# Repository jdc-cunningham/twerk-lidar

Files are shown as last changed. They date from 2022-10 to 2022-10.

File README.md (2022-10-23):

### Twerk Lidar Robot
A robot that utilizes onboard IMU and single-point lidar to navigate the world

#### With actual "Lidar"
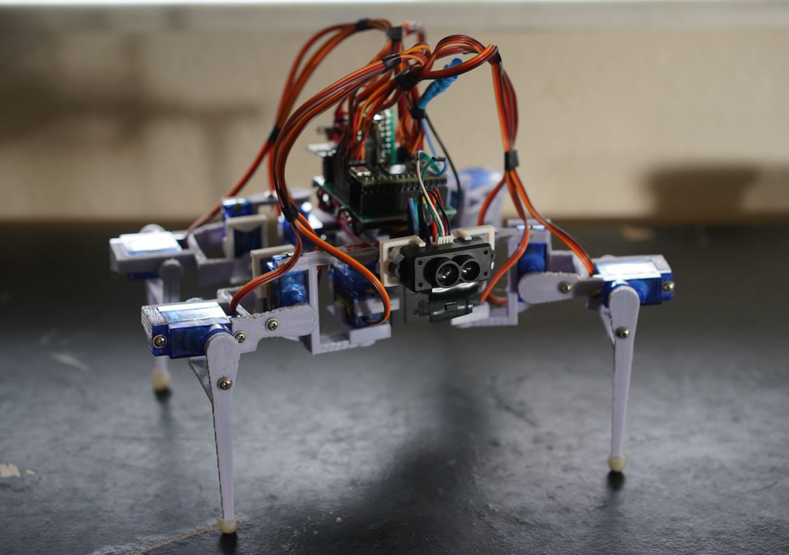
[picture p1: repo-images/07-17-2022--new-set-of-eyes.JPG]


#### Initial sensor setup
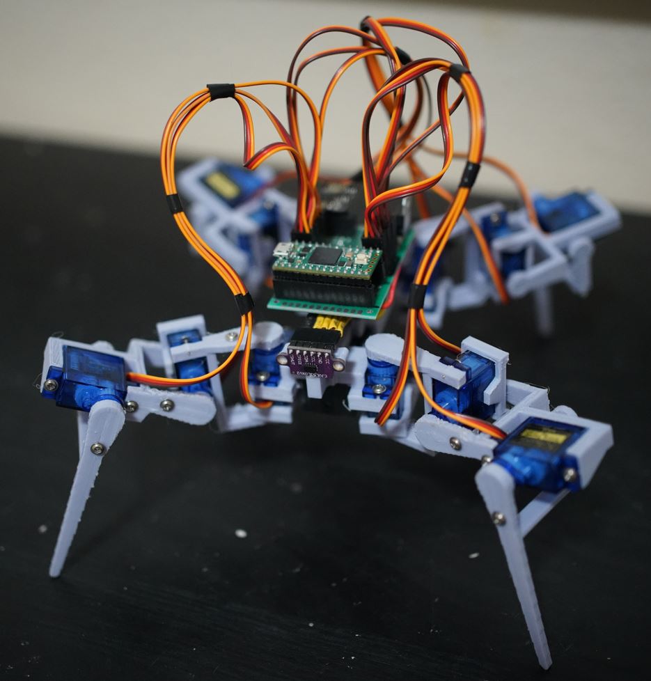
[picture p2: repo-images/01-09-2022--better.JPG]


### Project status (incomplete)

### What is it


Example depth map:
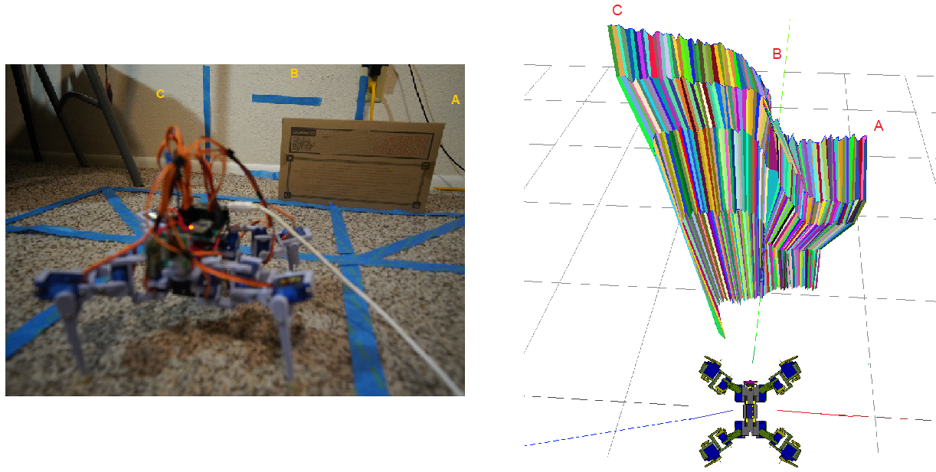
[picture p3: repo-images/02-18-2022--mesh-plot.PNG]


### Sensors

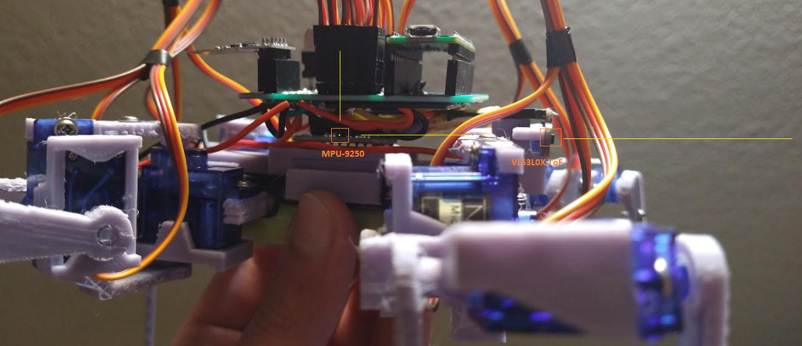
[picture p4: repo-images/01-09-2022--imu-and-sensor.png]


### Schematic

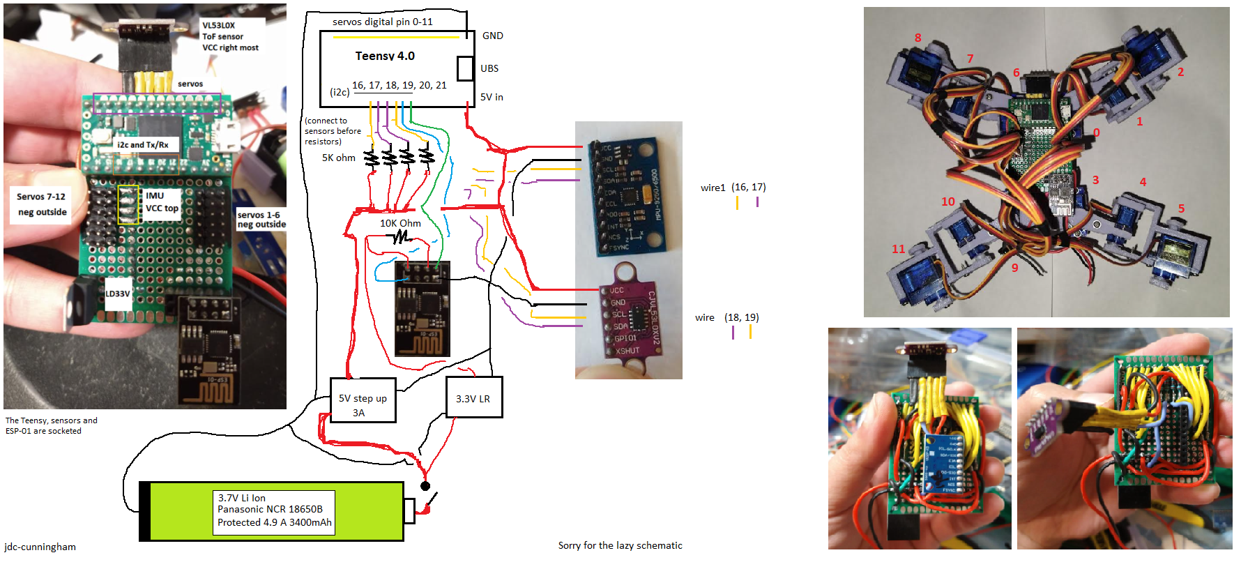
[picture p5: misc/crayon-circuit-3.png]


### Also Has 3D export/import from SketchUp to ThreeJS (GLB)

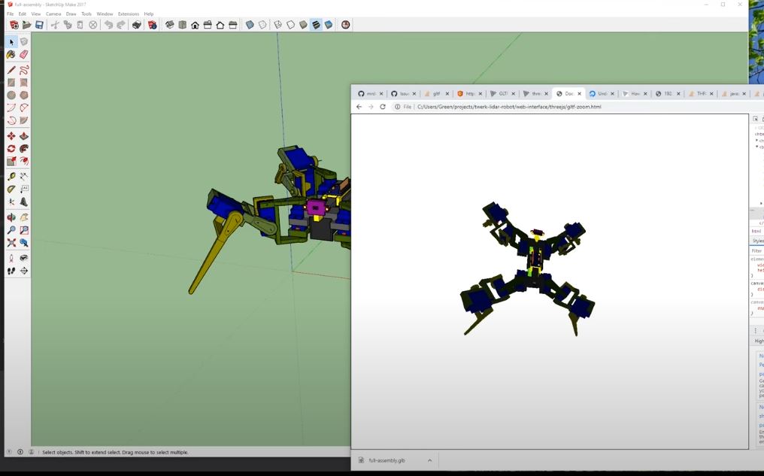
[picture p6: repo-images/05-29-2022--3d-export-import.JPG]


Uses Khronos glTF SketchUp plugin

### Unit cost estimate: $100+
This is a breakdown of the most expensive stuff on the robot. Does not include the little 3.3V regulator, the 3D printer itself, filament, proto-board, wire, etc...

* $24.00 - 12 x 9g servos
* $20.00 - Teensy 4.0
* $14.00 - MPU-9250
* $14.00 - MPS mEZD41503A-A 5V @ 3A DC/DC converter
* $11.00 - ToF sensor
* $10.00 - NCR 18650B 3.4 Ah 4.9A Protected Button Top Battery
* $3.25 - ESP-01

Upgrades (extra cost)
* $40.00 - TFMini-s Lidar
* $120 - 12 x MG90D metal gear servos

#### Note:

If you upgrade to the MG90D servos, you will need to add a separate power supply eg. MT3608 to power the Teensy so that the servos do not reset it while booting. Otherwise the legs will flail around on start up.

### Disclaimer - do not reproduce this project
While I have provided everything you need to make this robot, it is not intended to be rebuilt. This project suffers from mathematical inaccuracy both in the physical design and sensor accuracy. It was a good learning tool but this project is still a toy/not reliable to work autonomously.

TL;DR you buy cheap stuff you get cheap performance.

### Development environment

This was developed using Teensyduino so all of the libraries need to be installed there in order for the code to compile.
### Libraries used through Teensyduino IDE library search
* (I2C) IMU MPU9250 (Bolderflight set, check Readme in case more added)
  * MPU9250
  * Eigen
  * Units
* (I2C) ToF vl53l0x by Pololu

The TFmini-s is using raw serial

### Related software for this project
* Google SketchUp for the 3D modeling
* Cura for the slicer

### Related hardware
* Ender 3 Pro for the 3D printer

### About printing
The infill of prints are either 20% or 30%. I have sorted them in folders.

Pretty much anything brittle/small will be 30% or a major structural piece like the main chasis.

### Misc
This project borrows from my [first robot](https://github.com/jdc-cunningham/not-quite-an-ant-robot) with regard to how code is written.

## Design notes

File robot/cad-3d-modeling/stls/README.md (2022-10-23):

### Exploded view

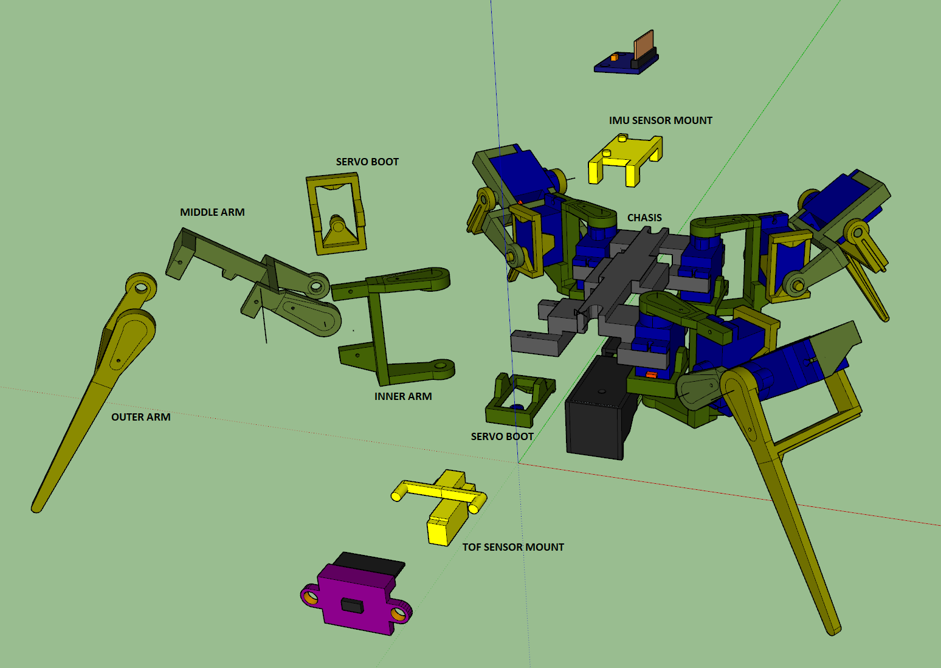
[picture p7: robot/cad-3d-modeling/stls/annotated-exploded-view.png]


### Print times
* 30% infill
  * chasis - 3 hrs
  * ToF sensor mount - 21 mins
  * Servo boot - 27 mins (need 8)
  * IMU sensor mount - 27 mins
* 20% infill (all together takes 2.5 hrs)
  * outer arm
  * middle arm
  * inner arm

### Assemby notes
For the outer-most arm, it is easier to pull it over the servo boot peg first, then over the servo arm. For the the middle arm it's easier to do the opposite, connect the servo arm first then pull it over the boot. Be careful with the boot peg as the printing is done in shear so it can snap easily.

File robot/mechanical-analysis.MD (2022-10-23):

### Servos and leg length

So far the robot weighs 7.2oz and that's just bare parts, no wires, plastic, nothing.

If it weighs 10oz then the arms should not be longer than 5 inches. That's too long really means can only lift like 3 oz.

Which you would think is plenty but my real robot it was weak and it weighs 10.7oz.



Oh... I did have a thought, when it's moving it will be on 3 legs usually. So the torque might get up to 3.3oz or more.

Yeah I think I need to keep it light and keep the servos close together.

Pulling servo torque data from this [video](https://www.youtube.com/watch?v=X5KyveL1cWc).

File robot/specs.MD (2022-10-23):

### Component weight
- 1.6oz - 18650
- 4.8oz - 9g servo x 12
- 0.1oz - Teensy 4.0
- 0.3oz - esp01 + boost converter + mpu9250 + tof sensor
- 0.2oz - battery holder
- 0.2oz - proto board

### Total weight
9.8oz

### Rough dimensions (due to front weight)
10" x 10" x 10"

### ToF sensor height from floor
3" and 6.5/16" or 3.38"

### ToF sensor distance from middle of body
2.5"

### Height from floor to pitch joints (middle servos)
2.5"

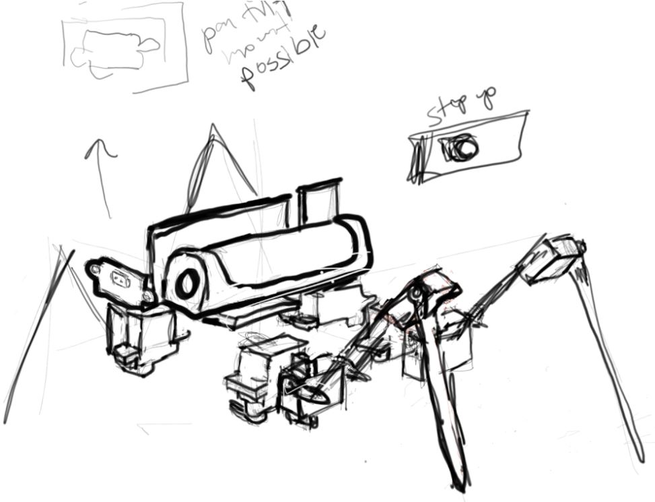
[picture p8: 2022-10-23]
twerk-lidar-robot-concept.JPG

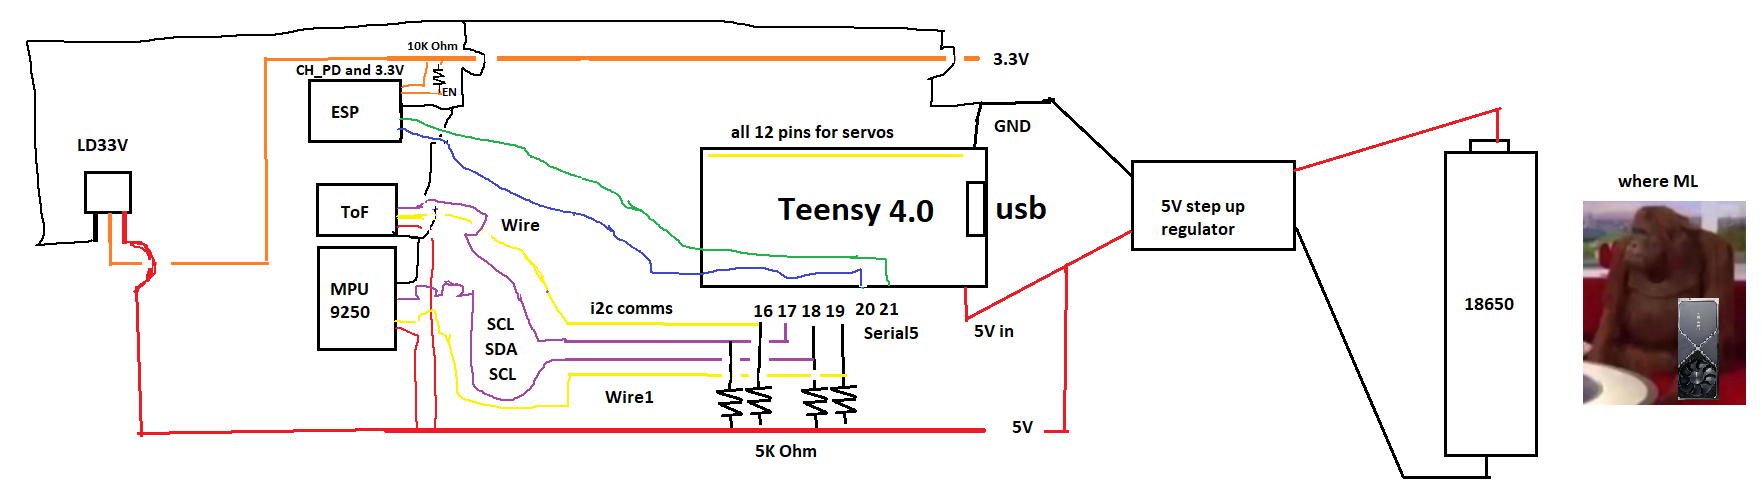
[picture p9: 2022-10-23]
misc/crayon-circuit-2.png

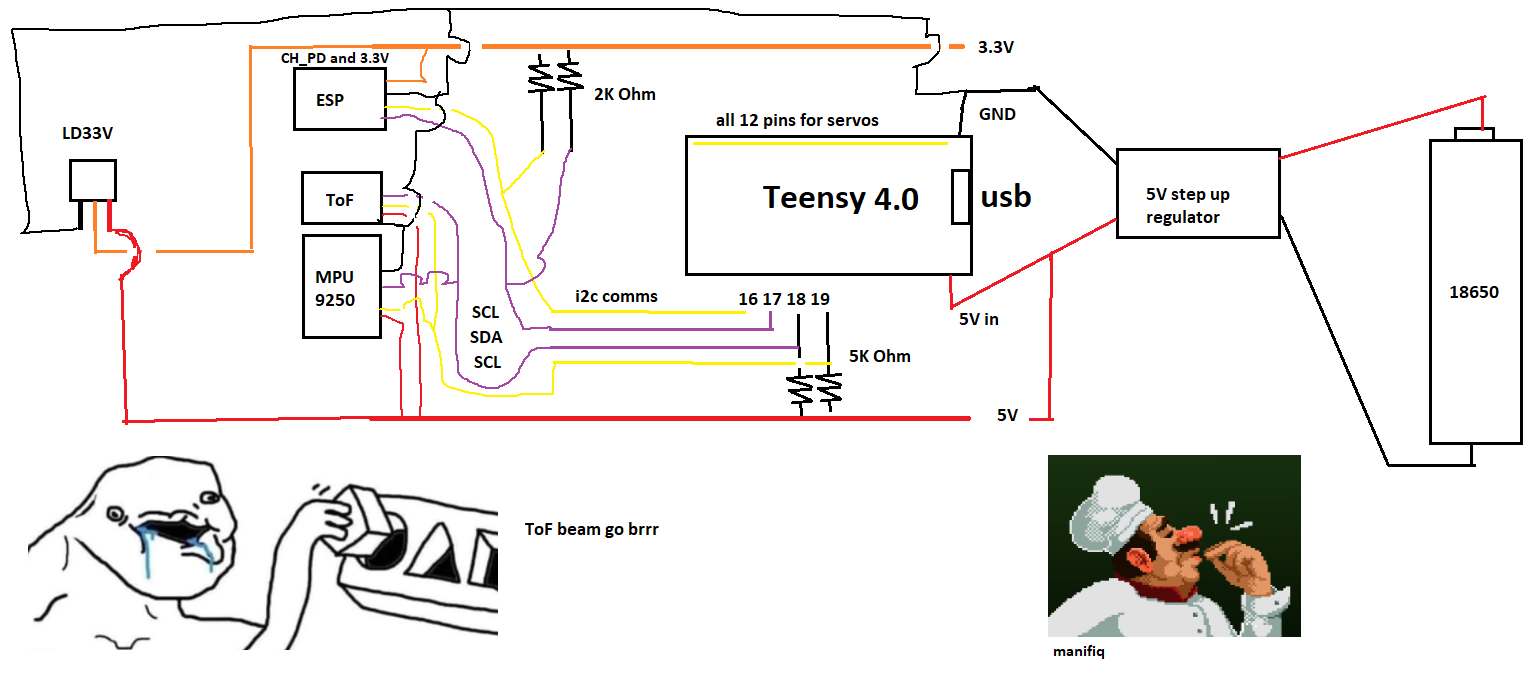
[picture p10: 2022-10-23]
misc/crayon-circuit.png

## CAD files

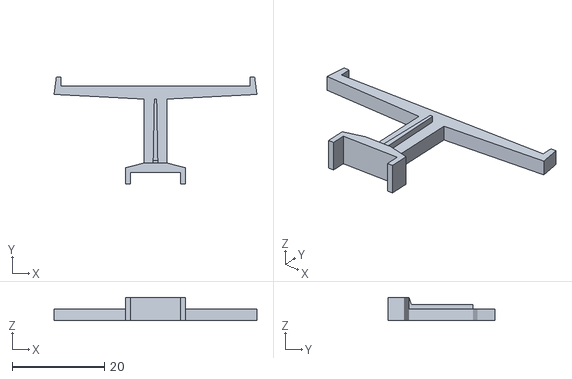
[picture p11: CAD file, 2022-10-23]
robot/cad-3d-modeling/stls/main-proto-board-stand.stl
44.0 x 23.3 x 5.08

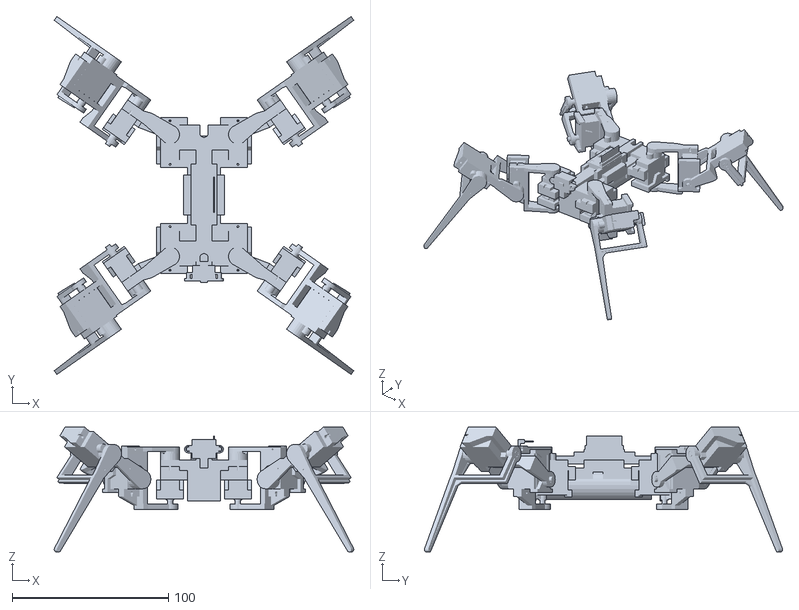
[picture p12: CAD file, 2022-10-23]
robot/cad-3d-modeling/stls/full-assembly.stl
191.5 x 228.8 x 79.8

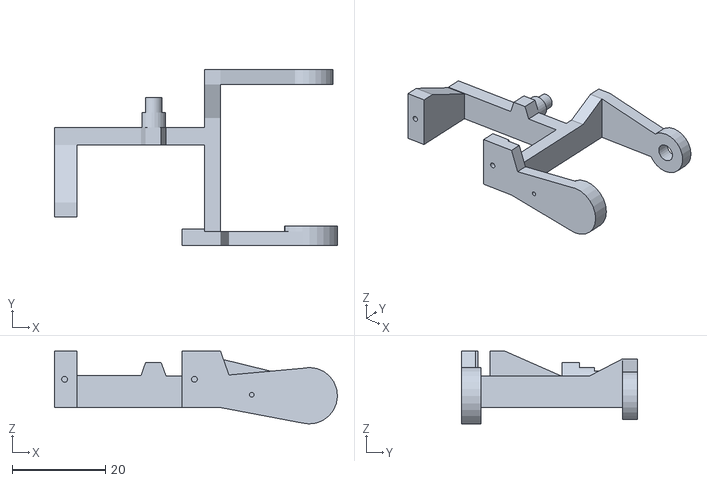
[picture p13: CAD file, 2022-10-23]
robot/cad-3d-modeling/stls/20-percent/back-right-middle-arm.stl
60.7 x 37.6 x 15.6

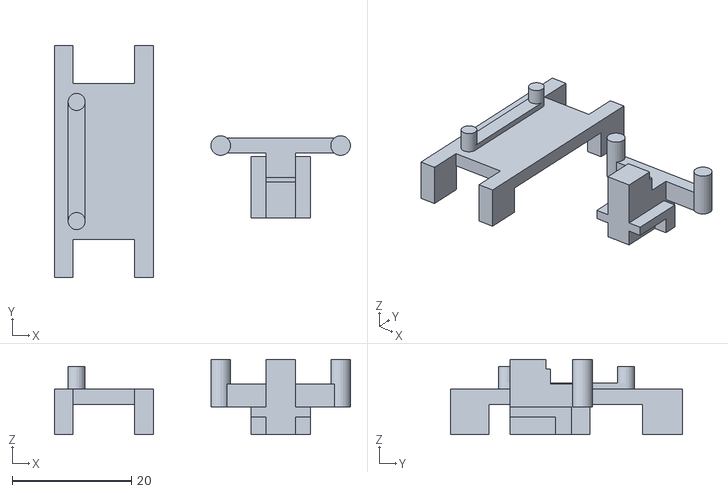
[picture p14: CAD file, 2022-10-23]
robot/cad-3d-modeling/stls/30-percent/sensor-mounts.stl
49.6 x 38.8 x 12.6

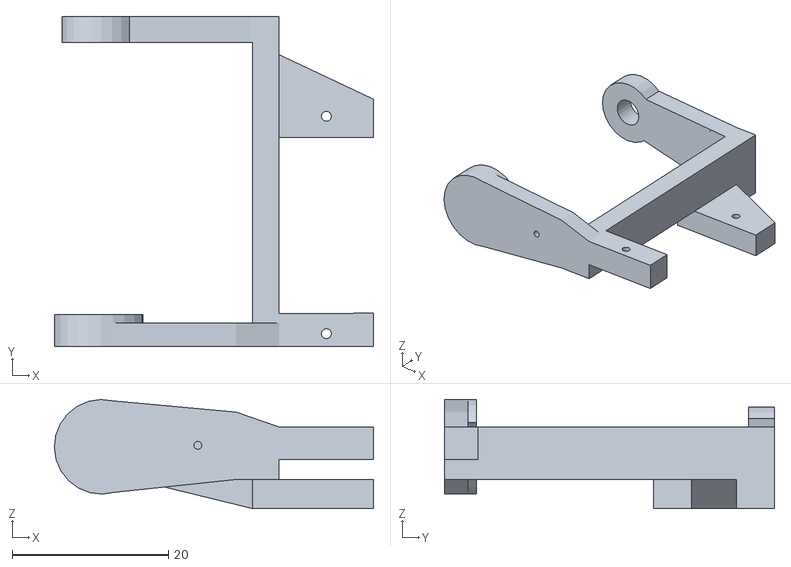
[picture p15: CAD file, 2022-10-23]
robot/cad-3d-modeling/stls/mg90d/mg90d-back-left-servo-arms--inner.stl
40.9 x 42.2 x 14.0

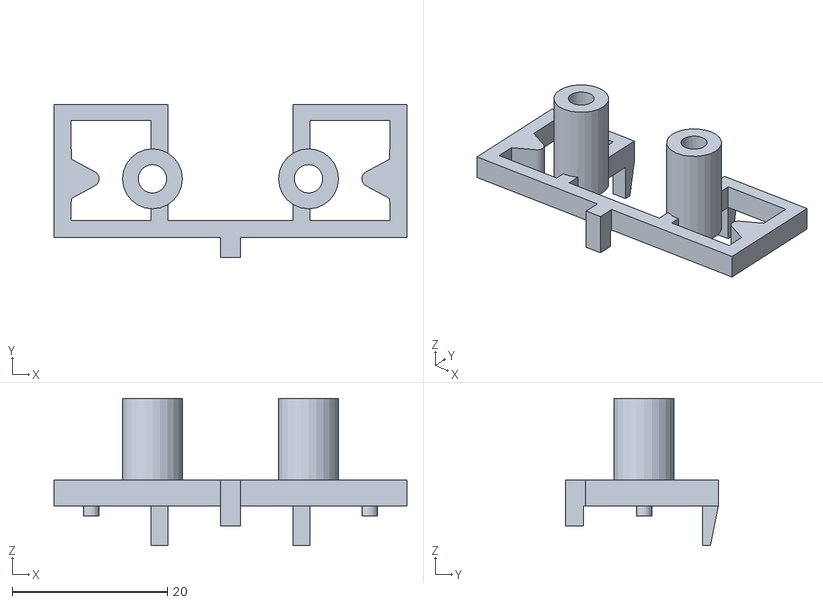
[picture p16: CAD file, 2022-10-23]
robot/cad-3d-modeling/stls/tfminis-mount-adapter.stl
45.4 x 19.6 x 18.9

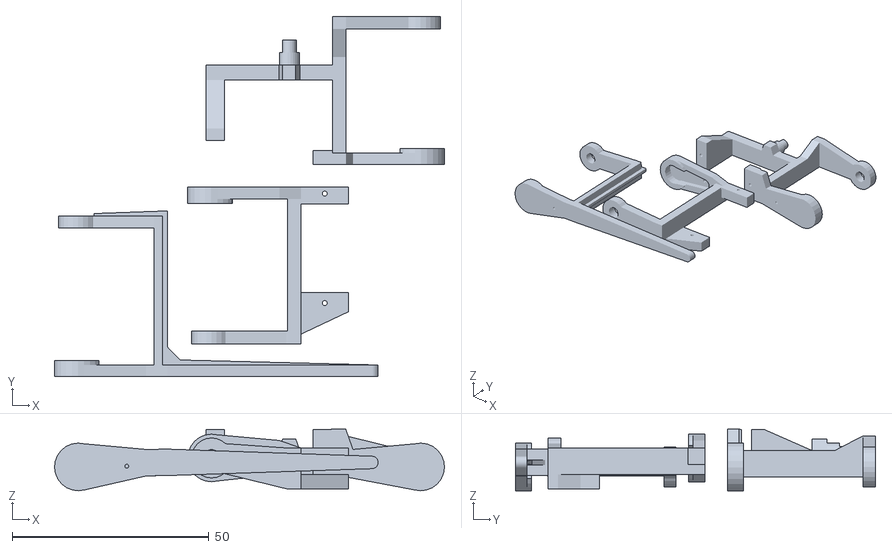
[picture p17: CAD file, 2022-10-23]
robot/cad-3d-modeling/stls/20-percent/back-right.stl
99.1 x 91.5 x 15.6

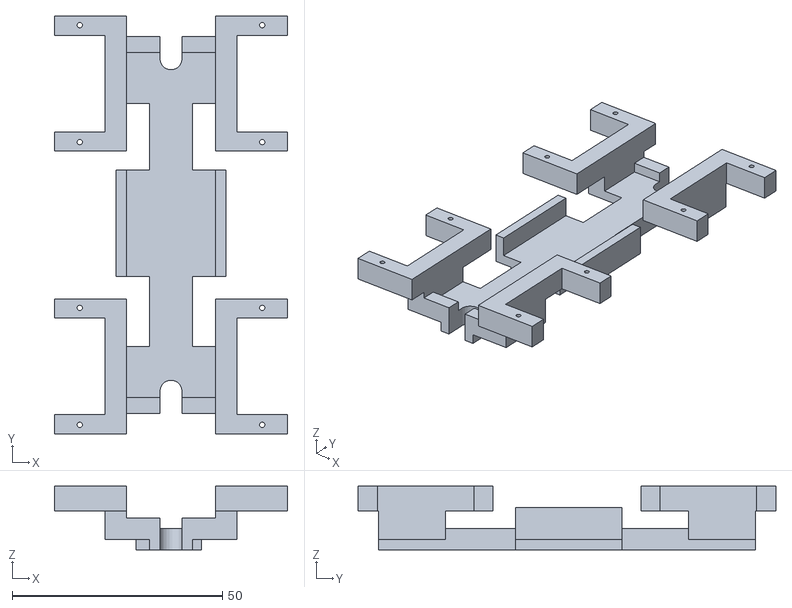
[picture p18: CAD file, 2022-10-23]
robot/cad-3d-modeling/stls/30-percent/chasis.stl
55.5 x 99.4 x 15.2

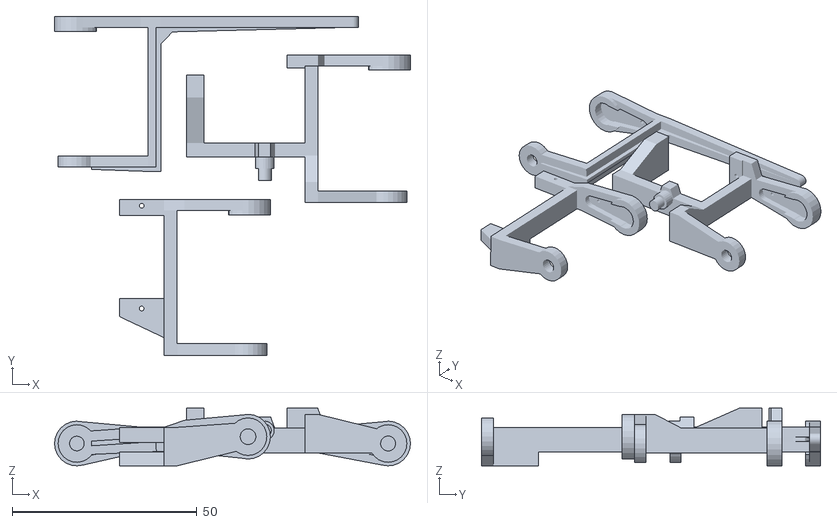
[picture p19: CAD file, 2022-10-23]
robot/cad-3d-modeling/stls/mg90d/setfr-front-right-servo-arms.stl
96.3 x 91.8 x 15.6

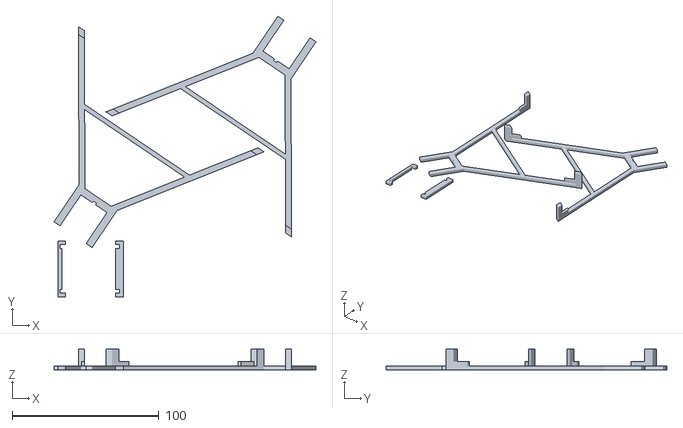
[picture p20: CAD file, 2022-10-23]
robot/cad-3d-modeling/stls/20-percent/project-stand.stl
178.3 x 191.0 x 14.0

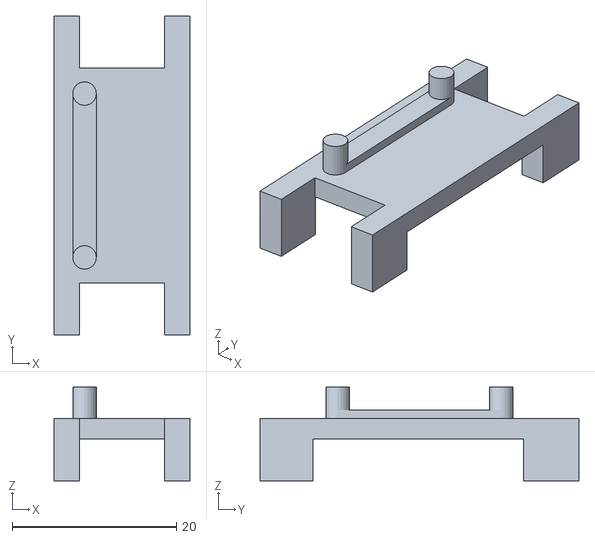
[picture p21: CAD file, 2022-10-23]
robot/cad-3d-modeling/stls/30-percent/imu-sensor-mount.stl
16.5 x 38.8 x 11.4

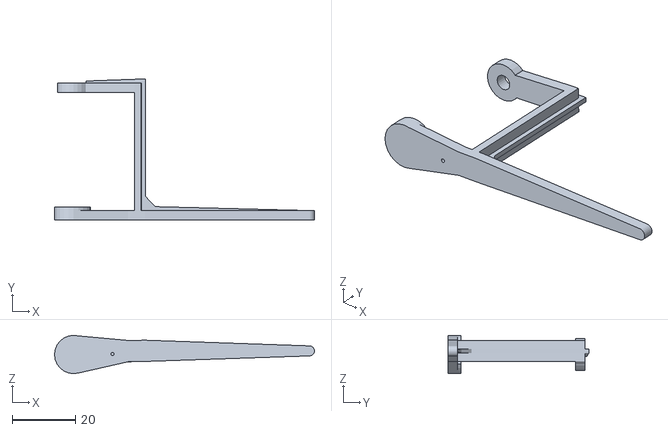
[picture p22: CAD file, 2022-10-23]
robot/cad-3d-modeling/stls/mg90d/brsa-outer.stl
82.2 x 44.6 x 12.1

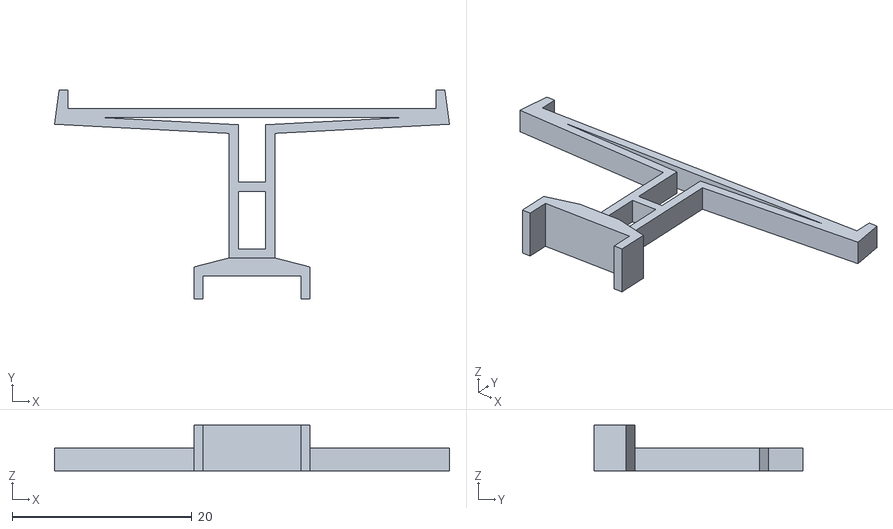
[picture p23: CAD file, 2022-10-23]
robot/cad-3d-modeling/stls/proto-board-stand-test.stl
44.0 x 23.3 x 5.08

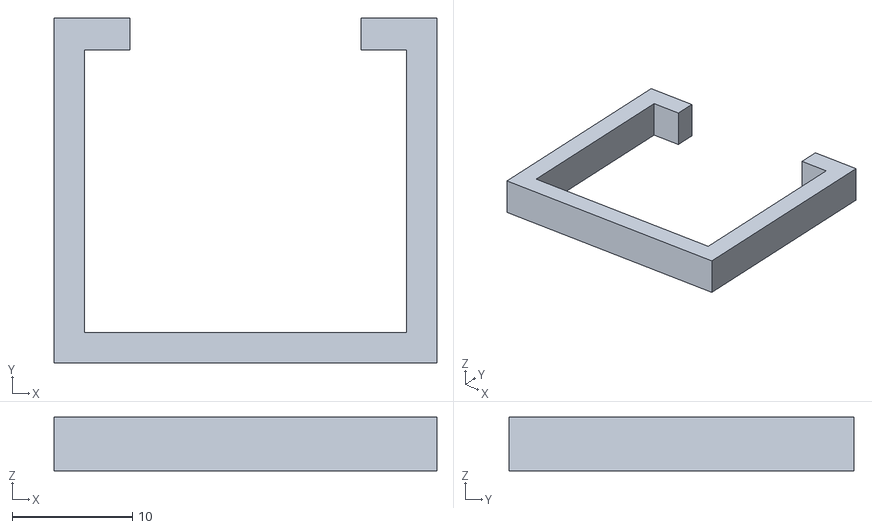
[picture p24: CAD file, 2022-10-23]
robot/cad-3d-modeling/stls/20-percent/battery-clip.stl
31.8 x 28.7 x 4.45

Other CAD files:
robot/cad-3d-modeling/stls/30-percent/tof-sensor-mount.stl
robot/cad-3d-modeling/stls/mg90d/flsa-outer.stl
robot/cad-3d-modeling/stls/power-supply-stand.stl
robot/cad-3d-modeling/stls/20-percent/back-left-servo-arms.stl
robot/cad-3d-modeling/sketchup/full-assembly.skp
robot/cad-3d-modeling/sketchup/mg90d-legs/back-left-servo-arms--inner.skp
robot/cad-3d-modeling/sketchup/mg90d-legs/back-left-servo-arms.skp
robot/cad-3d-modeling/sketchup/mg90d-legs/back-right-servo-arms.skp
robot/cad-3d-modeling/sketchup/mg90d-legs/front-left-servo-arms.skp
robot/cad-3d-modeling/sketchup/mg90d-legs/front-right-servo-arms.skp
robot/cad-3d-modeling/sketchup/mg90d-legs/servo-boot.skp
robot/cad-3d-modeling/sketchup/misc/angesl2.skp
robot/cad-3d-modeling/sketchup/misc/full-assembly--cones-not-lines.skp
robot/cad-3d-modeling/sketchup/misc/imu-plate.skp
robot/cad-3d-modeling/sketchup/misc/object-sampling.skp
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

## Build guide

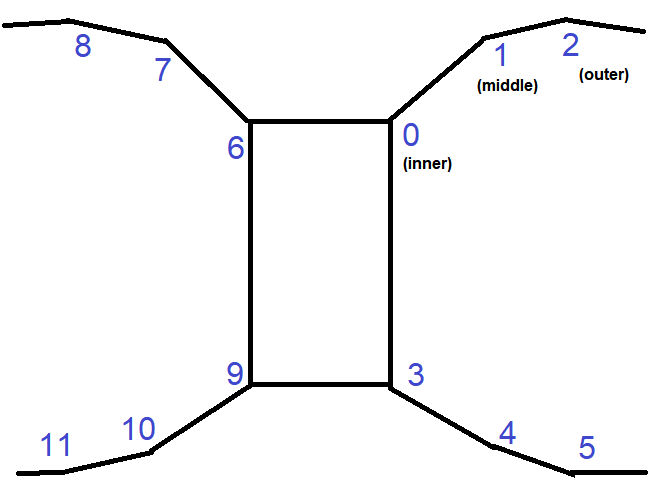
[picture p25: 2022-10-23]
robot/visual-servo-guide.png

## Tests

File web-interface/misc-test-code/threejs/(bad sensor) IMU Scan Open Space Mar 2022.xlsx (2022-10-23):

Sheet: Up 2
time ms | time s | servo pos | gyro time | gyro deg/s | elapsed time s |  |  | depth time | distance in | sweep angle | tof distance
11541 | 11.541 | 0 | 11541 | 0.24 | 0.027 | 0.00648 | 0.00648 | 11541 | 10.04 | 0.00648 | 10.04
11568 | 11.568 | 1 | 11568 | 0.67 | 0.027 | 0.01809 | 0.02457 | 11568 | 12.01 | 0.02457 | 12.01
11595 | 11.595 | 2 | 11595 | 4.39 | 0.027 | 0.11853 | 0.1431 | 11595 | 11.61 | 0.1431 | 11.61
11622 | 11.622 | 3 | 11622 | 7.81 | 0.027 | 0.21087 | 0.35397 | 11622 | 13.27 | 0.35397 | 13.27
11649 | 11.649 | 4 | 11649 | 21.85 | 0.027 | 0.58995 | 0.94392 | 11649 | 11.42 | 0.94392 | 11.42
11676 | 11.676 | 5 | 11676 | 16.3 | 0.027 | 0.4401 | 1.38402 | 11676 | 9.92 | 1.38402 | 9.92
11703 | 11.703 | 6 | 11703 | 17.88 | 0.027 | 0.48276 | 1.86678 | 11703 | 10.24 | 1.86678 | 10.24
11730 | 11.73 | 7 | 11730 | 26.73 | 0.027 | 0.72171 | 2.58849 | 11730 | 10.55 | 2.58849 | 10.55
11757 | 11.757 | 8 | 11757 | 27.83 | 0.027 | 0.75141 | 3.3399 | 11757 | 11.61 | 3.3399 | 11.61
11784 | 11.784 | 9 | 11784 | 20.26 | 0.027 | 0.54702 | 3.88692 | 11784 | 10.35 | 3.88692 | 10.35
11811 | 11.811 | 10 | 11811 | 26.73 | 0.027 | 0.72171 | 4.60863 | 11811 | 10.51 | 4.60863 | 10.51
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

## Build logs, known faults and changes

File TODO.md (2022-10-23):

### Initial poking around
- [x] upload code to Teensy
  - [x] try moving a servo
- [x] interface with MPU-9250
- [x] interface with single point lidar

### Design
- [x] mathematically determine ideal max weight of robot
  - went off dimensions and estimate of 10oz, trying to stay near 2" max moment arm length which should be 5oz/in torque
- [x] design body for servo placement
- [x] placement of parts based on size/wiring

### Basic obstacle detection
- [ ] come up with scan pattern/rules the robot follows
- [ ] add stuck catch, based on accel values
- [ ] mark objects as boxes if the sample beams hit anything

### Telemetry
- [ ] with ESP-01 send back data to remote thing that can create 3D world of what robot perceives
### Modeling
- [ ] create 3D world/mockup of robot
- [ ] simulate the navigation

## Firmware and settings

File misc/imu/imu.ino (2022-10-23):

/*
* Brian R Taylor
* brian.taylor@bolderflight.com
* 
* Copyright (c) 2021 Bolder Flight Systems Inc
*
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
* THE SOFTWARE IS PROVIDED “AS IS”, WITHOUT WARRANTY OF ANY KIND, EXPRESS OR
* IMPLIED, INCLUDING BUT NOT LIMITED TO THE WARRANTIES OF MERCHANTABILITY,
* FITNESS FOR A PARTICULAR PURPOSE AND NONINFRINGEMENT. IN NO EVENT SHALL THE
* AUTHORS OR COPYRIGHT HOLDERS BE LIABLE FOR ANY CLAIM, DAMAGES OR OTHER
* LIABILITY, WHETHER IN AN ACTION OF CONTRACT, TORT OR OTHERWISE, ARISING
* FROM, OUT OF OR IN CONNECTION WITH THE SOFTWARE OR THE USE OR OTHER DEALINGS
* IN THE SOFTWARE.
*/

#include "mpu9250.h"

/* Mpu9250 object, I2C bus,  0x68 address */
bfs::Mpu9250 imu(&Wire1, 0x68);

void setup() {
  /* Serial to display data */
  Serial.begin(115200);
  while(!Serial) {}
  /* Start the I2C bus */
  Wire1.begin();
  Wire1.setClock(400000);
  /* Initialize and configure IMU */
  if (!imu.Begin()) {
    Serial.println("Error initializing communication with IMU");
    while(1) {}
  }
  /* Set the sample rate divider */
  if (!imu.ConfigSrd(19)) {
    Serial.println("Error configured SRD");
    while(1) {}
  }
  Serial.println("good");
}

void loop() {
  /* Check if data read */
  if (imu.Read()) {
    // Serial.print(imu.new_imu_data());
    // Serial.print("\t");
    // Serial.print(imu.new_mag_data());
    // Serial.print("\t");
    // Serial.print(imu.accel_x_mps2());
    // Serial.print("\t");
    // Serial.print(imu.accel_y_mps2());
    // Serial.print("\t");
    Serial.print(imu.accel_z_mps2());
    // Serial.print("\t");
    // Serial.print(imu.gyro_x_radps());
    // Serial.print("\t");
    // Serial.print(imu.gyro_y_radps());
    // Serial.print("\t");
    // Serial.print(imu.gyro_z_radps());
    // Serial.print("\t");
    // Serial.print(imu.mag_x_ut());
    // Serial.print("\t");
    // Serial.print(imu.mag_y_ut());
    // Serial.print("\t");
    // Serial.print(imu.mag_z_ut());
    // Serial.print("\t");
    // Serial.print(imu.die_temp_c());
    Serial.print("\n");
  }
}

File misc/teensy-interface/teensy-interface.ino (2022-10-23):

#include "mpu9250.h"
#include <Wire.h>
#include <VL53L0X.h>

VL53L0X sensor;
bfs::Mpu9250 imu(&Wire1, 0x68);

void setupEsp() {

}

void setupTof() {
  Wire.begin();
  sensor.setTimeout(500);

  if (!sensor.init())
  {
    Serial.println("Failed to detect and initialize sensor!");
    while (1) {}
  }

  sensor.startContinuous();
}

float getTofSample() {
  sensor.startContinuous();
  float sample = sensor.readRangeContinuousMillimeters() * 0.0393701;
  sensor.stopContinuous();
  return sample;
}

void setupImu() {
  Serial.begin(115200);
  while(!Serial) {}
  Wire1.begin();
  Wire1.setClock(400000);
  /* Initialize and configure IMU */
  if (!imu.Begin()) {
    Serial.println("Error initializing communication with IMU");
    while(1) {}
  }
  /* Set the sample rate divider */
  if (!imu.ConfigSrd(19)) {
    Serial.println("Error configured SRD");
    while(1) {}
  }
}

void checkEspSerialMsg() {
  if (Serial5.available()) {
    Serial.print(Serial5.readString());
  }
}

void setupSerial() {
  Serial5.begin(115200);
}

void setup() {
  setupSerial();
  setupImu();
  setupTof();
}

void loop()
{
  if (imu.Read()) {
    Serial.print("imu y ");
    Serial.print(imu.accel_y_mps2());
    Serial.print("\t");
    Serial.print("tof in ");
    Serial.print(sensor.readRangeSingleMillimeters() * 0.0393701);
    Serial.println("");
  }

  // send/receive test ws socket
  // if (imu.Read())
  // {
  //   checkEspSerialMsg();
  //   Serial5.print(imu.accel_z_mps2());
  //   Serial5.print(",");
  //   Serial5.print(sensor.readRangeSingleMillimeters() * 0.0393701);
  // }

  delay(100);
}

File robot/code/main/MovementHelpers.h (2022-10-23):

/**
 * @brief Get the Servo By Pin object
 * 
 * @param digitalPin 
 * @return struct
 */
Servo getServoByPin(int digitalPin)
{
  if (digitalPin == 0) // ugh this sucks
  {
    return frontRightInnerJoint.servo;
  } else if (digitalPin == 1)
  {
    return frontRightMiddleJoint.servo;
  } else if (digitalPin == 2)
  {
    return frontRightOuterJoint.servo;
  } else if (digitalPin == 3)
  {
    return backRightInnerJoint.servo;
  } else if (digitalPin == 4)
  {
    return backRightMiddleJoint.servo;
  } else if (digitalPin == 5)
  {
    return backRightOuterJoint.servo;
  } else if (digitalPin == 6)
  {
    return frontLeftInnerJoint.servo;
  } else if (digitalPin == 7)
  {
    return frontLeftMiddleJoint.servo;
  } else if (digitalPin == 8)
  {
    return frontLeftOuterJoint.servo;
  } else if (digitalPin == 9)
  {
    return backLeftInnerJoint.servo;
  } else if (digitalPin == 10)
  {
    return backLeftMiddleJoint.servo;
  } else
  {
    return backLeftOuterJoint.servo;
  }
}

joint getJointByPin (int digitalPin)
{
  if (digitalPin == 0) // ugh this sucks
  {
    return frontRightInnerJoint;
  } else if (digitalPin == 1)
  {
    return frontRightMiddleJoint;
  } else if (digitalPin == 2)
  {
    return frontRightOuterJoint;
  } else if (digitalPin == 3)
  {
    return backRightInnerJoint;
  } else if (digitalPin == 4)
  {
    return backRightMiddleJoint;
  } else if (digitalPin == 5)
  {
    return backRightOuterJoint;
  } else if (digitalPin == 6)
  {
    return frontLeftInnerJoint;
  } else if (digitalPin == 7)
  {
    return frontLeftMiddleJoint;
  } else if (digitalPin == 8)
  {
    return frontLeftOuterJoint;
  } else if (digitalPin == 9)
  {
    return backLeftInnerJoint;
  } else if (digitalPin == 10)
  {
    return backLeftMiddleJoint;
  } else
  {
    return backLeftOuterJoint;
  }
}

/**
 * @brief this function is a wrapper around Joint.write() however
 * it checks against the servo's min/max throws based on robot geometry
 * the min/max values are determined upon assembling the robot/calibrated
 * manually since the servos have not feedback
 * 
 * @param servo 
 * @param deg 
 */
void safeServoWrite(int servoPin, int deg)
{
  joint jointToMove = getJointByPin(servoPin);
  int servoMin = jointToMove.minPos;
  int servoMax = jointToMove.maxPos;

  if (deg <= servoMax && deg >= servoMin)
  {
    jointToMove.servo.write(deg);
  }
}

/**
 * This function moves servos together at the same speed
 * there is a "bias" where the shortest motion will end first
 * @param {int} - array of arrays with the following: servo enum, start pos, end pos
 * @param {int} - array length
 * @param {int} - duration of motion in ms
 */
void moveServos(int servoGroupArr[][3], int servoGroupArrLen, int motionDuration)
{
  /**
   * loop through servos, find largest range between start/end pos
   * there is no error checking, I find coding in Arduino to be cumbersome */
  motionInProgress = true;
  int largestServoRange = 0;

  // emergency stop
  if (stopRobot)
  {
    return;
  }

  for (int servoGroupIndex = 0; servoGroupIndex < servoGroupArrLen; servoGroupIndex++) {
    int range = 0;
    if (servoGroupArr[servoGroupIndex][1] < servoGroupArr[servoGroupIndex][2]) {
      // increase
      range = servoGroupArr[servoGroupIndex][2] - servoGroupArr[servoGroupIndex][1];
      if (range > largestServoRange) {
        largestServoRange = range;
      }
    } else
    {
      // decrease
      range = servoGroupArr[servoGroupIndex][1] - servoGroupArr[servoGroupIndex][2];
      if (range > largestServoRange) {
        largestServoRange = range;
      }
    }
  }

  /* do the motion on the servos going by largest range
   * this will update all the servo positions at the same rate
   * but some will finish earlier than others if the motion range is not the same */
  for (int pos = 0; pos < largestServoRange; pos++) {
    for(int servoGroupIndex = 0; servoGroupIndex < servoGroupArrLen; servoGroupIndex++) {
      int servoPin = servoGroupArr[servoGroupIndex][0];
      joint jointToMove; // this is like this to avoid a warning unused variable
      jointToMove = getJointByPin(servoGroupArr[servoGroupIndex][0]); // sucks double lookup
      int nextServoPos;

      if (servoGroupArr[servoGroupIndex][1] < servoGroupArr[servoGroupIndex][2]) {
        // increase
        if (servoGroupArr[servoGroupIndex][1] + pos < servoGroupArr[servoGroupIndex][2]) {
          nextServoPos = servoGroupArr[servoGroupIndex][1] + pos;
          safeServoWrite(servoPin, nextServoPos);
        }
      } else
      {
        // decrease
        if (servoGroupArr[servoGroupIndex][1] - pos > servoGroupArr[servoGroupIndex][2]) {
          nextServoPos = servoGroupArr[servoGroupIndex][1] - pos;
          safeServoWrite(servoPin, nextServoPos);
        }
      }

      // update global servo current position
      jointToMove.currentPos = nextServoPos;
    }

    int timeNow = millis();

    // track robot trajectory over time
    if (trackImu)
    {
      if (imu.Read())
      {
        motionImuTracking[timeNow] = {
          roundUp(imu.accel_x_mps2()),
          roundUp(imu.accel_y_mps2()),
          roundUp(radianToDegree(imu.gyro_z_radps()))
        };
      } else
      {
        motionImuTracking[timeNow] = {
          0.0, // to see how many are missed
          0.0,
          0.0
        };
      }
    }

    if (performScan && !obstacleFound)
    {
      float tofSampleIn = 0.00;
      float tfMiniSDistance = 0.00;

      int midPos = (largestServoRange - 1) / 2;
      int lowMidPos = midPos / 2; // this is expecting to truncate floats
      int highMidPos = (largestServoRange - 1) - lowMidPos;

      // ToF ranging sensor
      if (
        pos == 0 || pos == midPos
        || pos == lowMidPos || pos == highMidPos
        || (pos == largestServoRange - 1)
      ) // scan 5 samples per plane, not happening here no overlap check
      {
        // scanCounter += 1;
        tofSampleIn = getTofDistanceCorrected();

        // short circuit
        if (tofSampleIn < 5) // not able to move forward must turn
        {
          obstacleFound = true;
        }

        if (!obstacleFound && activeScan == "tilt-up-2")
        {
          if (u2Smallest == 0.0) // can turn this block into a function
          {
            u2Smallest = tofSampleIn;
          } else if (tofSampleIn < u2Smallest)
          {
            u2Smallest = tofSampleIn;
          }
        }

        if (!obstacleFound && activeScan == "tilt-up-1")
        {
          if (u1Smallest == 0.0)
          {
            u1Smallest = tofSampleIn;
          } else if (tofSampleIn < u1Smallest)
          {
            u1Smallest = tofSampleIn;
          }
        }

        if (!obstacleFound && activeScan == "middle")
        {
          if (mSmallest == 0.0)
          {
            mSmallest = tofSampleIn;
          } else if (tofSampleIn < mSmallest)
          {
            mSmallest = tofSampleIn;
          }
        }
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

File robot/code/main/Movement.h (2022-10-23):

#include "MovementHelpers.h"

void centerAllLegs()
{
  frontRightInnerJoint.servo.write(frontRightInnerJoint.startPos);
  frontRightMiddleJoint.servo.write(frontRightMiddleJoint.startPos);
  frontRightOuterJoint.servo.write(frontRightOuterJoint.startPos);
  backRightInnerJoint.servo.write(backRightInnerJoint.startPos);
  backRightMiddleJoint.servo.write(backRightMiddleJoint.startPos);
  backRightOuterJoint.servo.write(backRightOuterJoint.startPos);
  frontLeftInnerJoint.servo.write(frontLeftInnerJoint.startPos);
  frontLeftMiddleJoint.servo.write(frontLeftMiddleJoint.startPos);
  frontLeftOuterJoint.servo.write(frontLeftOuterJoint.startPos);
  backLeftInnerJoint.servo.write(backLeftInnerJoint.startPos);
  backLeftMiddleJoint.servo.write(backLeftMiddleJoint.startPos);
  backLeftOuterJoint.servo.write(backLeftOuterJoint.startPos);
}

/**
 * these are attached with regard to the board's design
 * where the right half of the robot pins are on the right side, etc...
 * also it goes inner out
 */
void setAndCenterServos()
{
  frontRightInnerJoint.servo.attach(0);
  frontRightMiddleJoint.servo.attach(1);
  frontRightOuterJoint.servo.attach(2);
  backRightInnerJoint.servo.attach(3);
  backRightMiddleJoint.servo.attach(4);
  backRightOuterJoint.servo.attach(5);
  frontLeftInnerJoint.servo.attach(6);
  frontLeftMiddleJoint.servo.attach(7);
  frontLeftOuterJoint.servo.attach(8);
  backLeftInnerJoint.servo.attach(9);
  backLeftMiddleJoint.servo.attach(10);
  backLeftOuterJoint.servo.attach(11);

  // neutral stance
  centerAllLegs();
}

/**
 * @brief this function is used to move the servos by a web interface
 * this one does not use safeServoWrite, since it's primarily used to
 * determine the min, max endpoints
 * 
 * espMsg pattern msc_servoInt__deg
 */
void manualMoveServo(String espMsg)
{
  int degStart = espMsg.indexOf("__");
  int servoPin = espMsg.substring(4, degStart).toInt();
  int servoDeg = espMsg.substring(degStart + 2).toInt();
  Servo servoToMove = getServoByPin(servoPin);
  servoToMove.write(servoDeg);
}

// based on visual observation of Regis Hsu 2017 spider bot
void moveForward5()
{
  // these motions could specify degree, dir and use global to know where servo is
  mf5MoveFrontRightLegUp();
  mf5MoveFrontRightLegForward();
  mf5MoveFrontRightLegDownFromUp();

  // sampleYAccel = true;
  trackImu = true;
  mf5PullForwardRight();
  sampleYAccel = false;
  trackImu = false;

  mf5MoveBackLeftLegUp();
  mf5MoveBackLeftLegForward();
  mf5MoveBackLeftLegDownFromUp();

  mf5MoveFrontLeftLegUp();
  mf5MoveFrontLeftLegForward();
  mf5MoveFrontLeftLegDownFromUp();

  // sampleYAccel = true;
  trackImu = true;
  mf5PullForwardLeft();
  sampleYAccel = false;
  trackImu = false;

  mf5MoveBackRightLegUp();
  mf5MoveBackRightLegForward();
  mf5MoveBackRightLegDownFromUp();

  // updateTelemetry("mf");
}

// also based on Regis Hsu 2017 spider robot turn gait
void turnLeft()
{
  mf5MoveFrontRightLegUp();
  // sampleGyroZ = true;
  leftTurnPivot();
  // sampleGyroZ = false;
  mf5MoveFrontRightLegDownFromUp();

  mf5MoveFrontLeftLegUp();
  leftTurnPivot2();
  mf5MoveFrontLeftLegDownFromUp();

  mf5MoveBackLeftLegUp();
  // sampleGyroZ = true;
  leftTurnPivot3();
  // sampleGyroZ = false;
  mf5MoveBackLeftLegDownFromUp();

  // at 45 deg here
  // rest below returns to neutral

  mf5MoveBackRightLegUp();
  ltp3ToNeutral();
  mf5MoveBackRightLegDownFromUp();

  mf5MoveFrontRightLegUp();
  ltp3ToNeutral2();
  mf5MoveFrontRightLegDownFromUp();

  // increment rotation
  robotHeading -= 56.3;

  // updateTelemetry("tl");
}

void turnRight()
{
  
  
}
